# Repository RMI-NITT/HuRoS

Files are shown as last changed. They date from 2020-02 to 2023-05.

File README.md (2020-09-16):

# HuRoS
A 10 DoF Bipedal Walking robot, to be developed as a platform for further research on design and control of humanoid robots.

* 3D Printer -> Contains all the CAD files of the parts which were 3D printed for fabrication.
* CODES -> Contains all the motor control and simulation codes.
* References -> papers related to humaniod robots
* 100rpm_RMCS-3013.pdf;60rpm_RMCS-3012.pdf -> motors used in HuRoS-data sheet
* Dual_DC_Motor_Driver_20A.pdf -> motor drivers used 
* Biped Recent picture.jpeg -> complete fabrication 

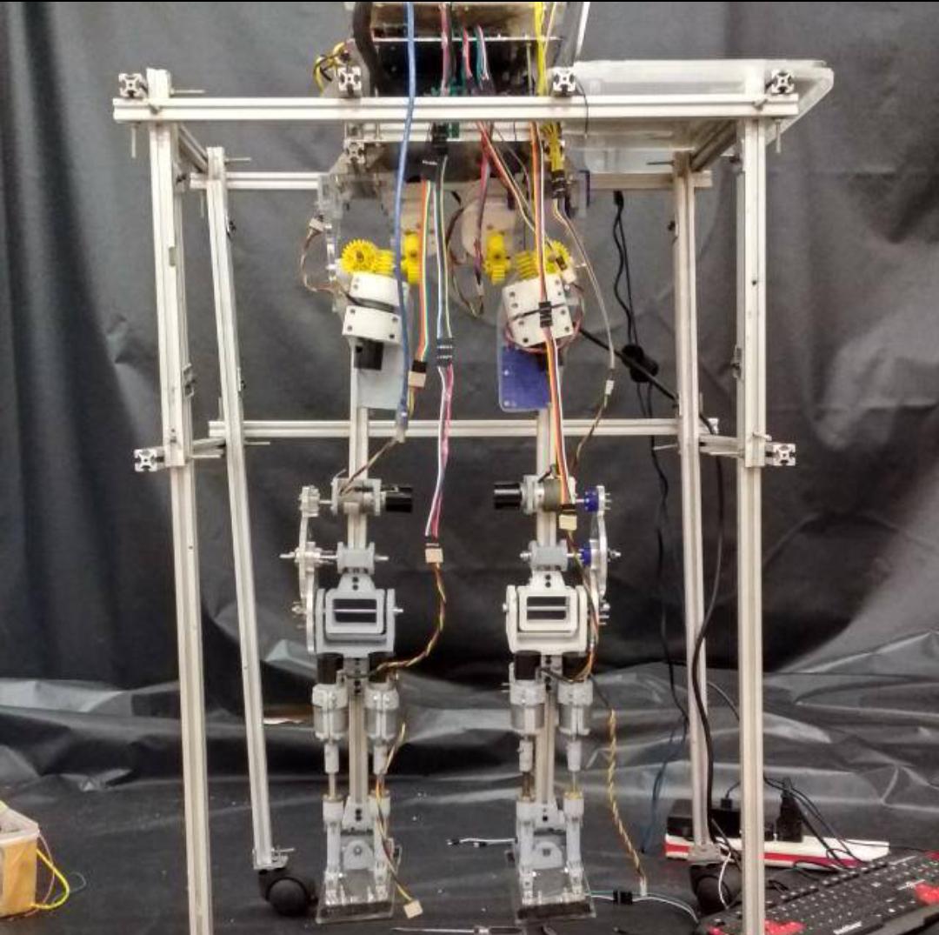
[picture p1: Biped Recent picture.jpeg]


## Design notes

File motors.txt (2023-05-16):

HuRoS motors and power supply

Rhino motor - RMCS 3013 DC geared motor with quad encoder, 100RPM 12V, 10 nos
Rated voltage - 12V, 
Running current - 0.8A/1.04A,
Starting peak current - 7.5A

Corsair VS550 power supply
GND the Green wire in motherboard connector for by-passing

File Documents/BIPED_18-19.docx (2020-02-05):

BIPED

Problem Statement

Simulate and fabricate bipedal robot which can walk over flat terrain by implementing CoM based and ZMP based control and stability techniques.

Tasks to be done

- Design an actuation mechanism for a universal joint. These types of joints are placed at each ankle and hip joints.
- Simulation of static stable gait in ROS-gazebo.
- Design and Fabrication of optimised model for improved agility and efficiency.
- Developing a dynamic model using Lagrangian mechanics.
- Simulation of dynamic gait using non-linear control strategies like SMC, Backstepping, etc

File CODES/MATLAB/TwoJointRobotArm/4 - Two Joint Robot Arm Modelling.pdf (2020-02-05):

## Two Joints Robot Arm Dynamics

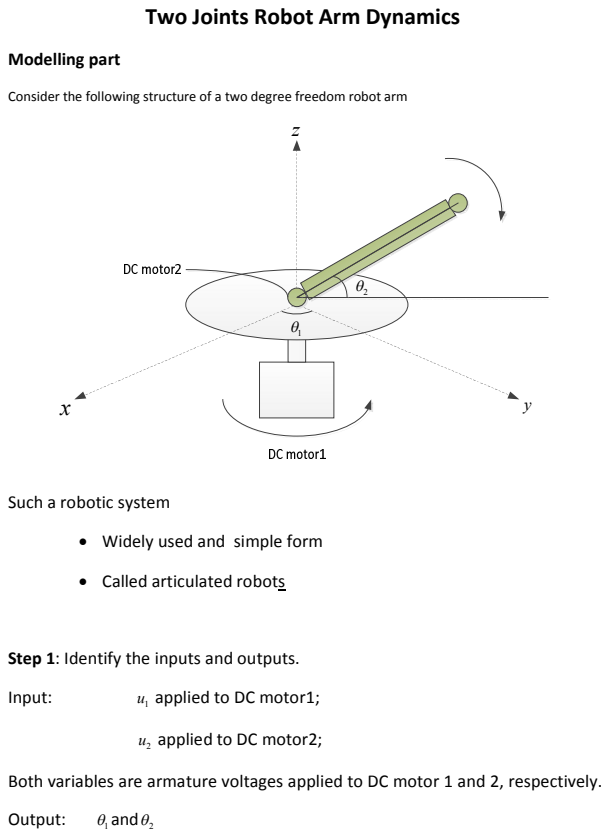
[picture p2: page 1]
Modelling part; Input:; Output:; θ1 andθ2

Consider the following structure of a two degree freedom robot arm

Such a robotic system

• Widely used and simple form

• Called articulated robots

Step 1: Identify the inputs and outputs.

u applied to DC motor1;

u applied to DC motor2;

Both variables are armature voltages applied to DC motor 1 and 2, respectively.

*Notations*

Shaft of DC motor1, it has a fixed part of the inertia 0

J that is obtained by

taking the arm away.

In terms of the robot arm, it has length H and mass m , i.e. { H , m } .

The parameters of the DC motors are given by:

DC motor1Þ | 1 | 1
1 | 1 | 1 | 2 { , , | , | } R L K K

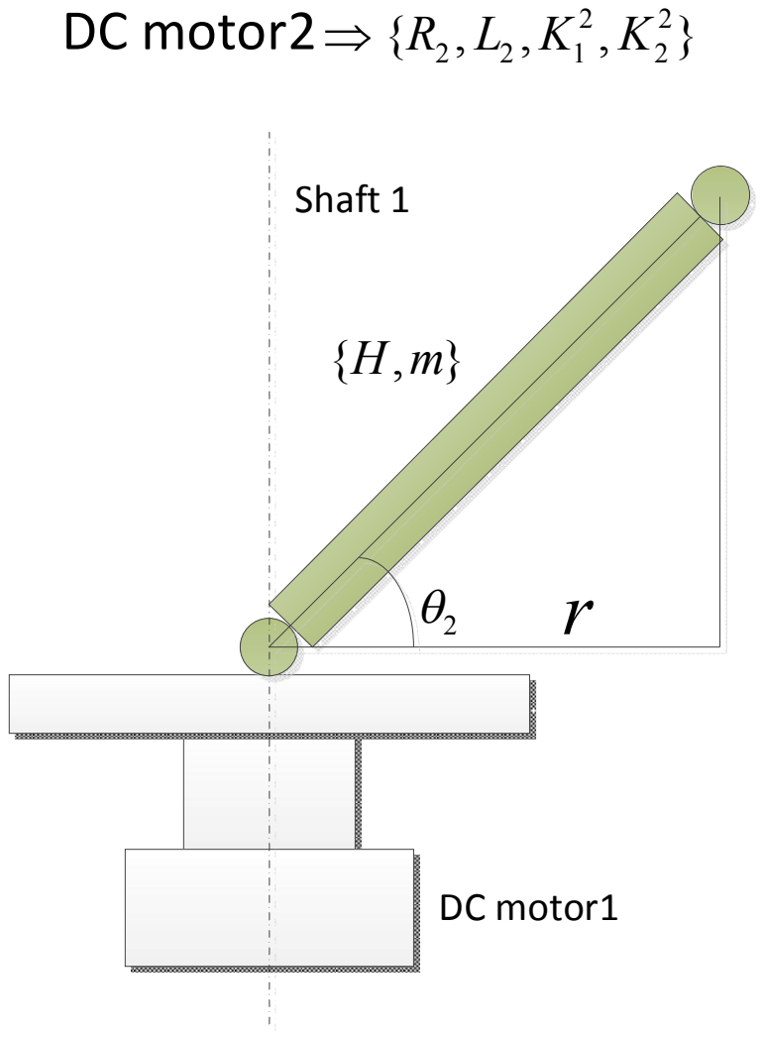
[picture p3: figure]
DC motor2Þ; Shaft 1; DC motor1

The equivalent inertia for the shaft driven by DC motor 1 is given by

2 | 2 | 2
0 | 0 | 2
1 | 1
cos
2 | 2
J | mr | J | mH + | = | + | θ | (1)

Therefore the mechanical equation for DC motor1 (shaft1) is

2
2 | 2 | 1 1
0 | 2 | 2 1 2

1
cos
2

d
J | mH | K i
dt

θ
θ
é | ù
+ | = ê | ú ë | û | (2)

where 1

i is the armature current of DC motor1.

1 | 1 1
1 1 | 1 | 1 | 1
di | d R i | L | K | u
dt | dt

θ
+ | + | = | (3)

Equation (3) is the electrical equation for the armature circuit of DC motor1.

Robot arm part modelling (DC motor2)

2
2 | 2
2 | 2 2 | 2 2
2 | 2 2
2 2 | 2 | 1 | 2

1
cos
2

d
J | K i | mHg
dt
di | d R i | L | K | u
dt | dt

θ
θ

θ

ì
= - ï
ï
í
ï | + | + | = ïî

(4)

Therefore the mechanical part of the model can be expressed as the following matrix form

2
1
2 | 2 | 1 2
0 | 2 | 2 | 1
2 | 2
2 | 2 | 2 | 2
2
2
1 | 0
cos | 0 | 0
( ) | 2 | 1
0 | cos 0 | 2

d
J | mH | dt | K | i
M q
d | K | i | Hmg J
| | dt θ
θ
θ | θ
é | ù é | ù | é | ù ê | ú + | é | ùé ù ê | ú | ê | ú = | = | + ê | ú ê | úê ú ê | úê | ú | ë û ê | ú - ë | û ë | û | ë | û ê | ú ë | û | (5)

In the course work the left hand side of the above equation is extended to: M (q,q) which is defined as inertia matrix for general multiple joint robot arm.

The above system can also be expressed as a state space form described before.

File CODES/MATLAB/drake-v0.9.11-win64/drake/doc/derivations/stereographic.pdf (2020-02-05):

## Stereographic Projection

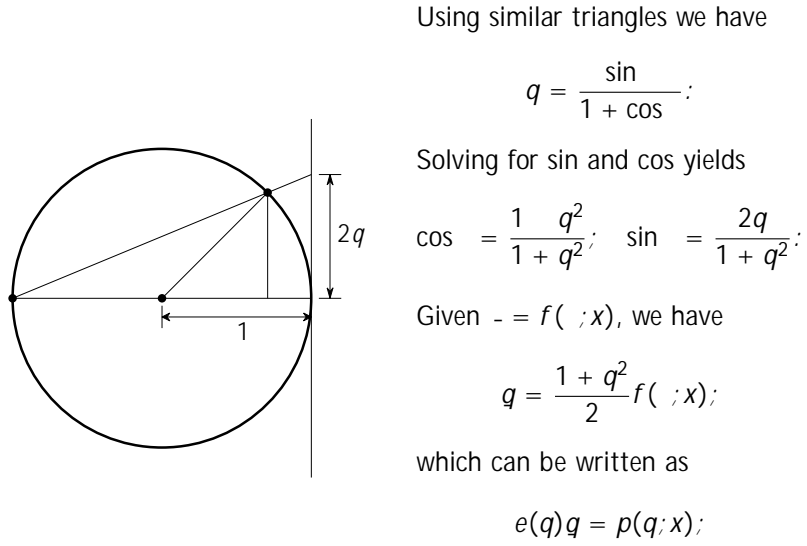
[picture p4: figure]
Using similar triangles we have; sin 1 + cos :; Solving for sin and cos yields; cos =; ; sin =; Given _ = f (; x), we have; which can be written as

with e() and p() polynomial in q.

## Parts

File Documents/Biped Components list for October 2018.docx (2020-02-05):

Biped Components list for October 2018

Component | Quantity | Cost per item | Cost | Link
Motor with encoders {HIGH TORQUE (35kgcm) QUAD ENCODER GEARED DC MOTOR 12V 100RPM} | 3 | 2124 | 6372 | https://robokits.co.in/motors/encoder-dc-servo/high-torque-quad-encoder-geared-dc-motor-12v-100rpm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
Motor driver {DUAL DC MOTOR DRIVER 20A} | 2 | 767 | 1534 | https://robokits.co.in/motor-drives/dual-dc-motor-driver-20a
Fabrication Parts (Aluminuim T Slot sections, L shaped aluminium reinforcements, 3 mm Aluminium 70755 Sheets, 3D printed parts,fasteners,etc) | | | 4000
Total | | | 11900

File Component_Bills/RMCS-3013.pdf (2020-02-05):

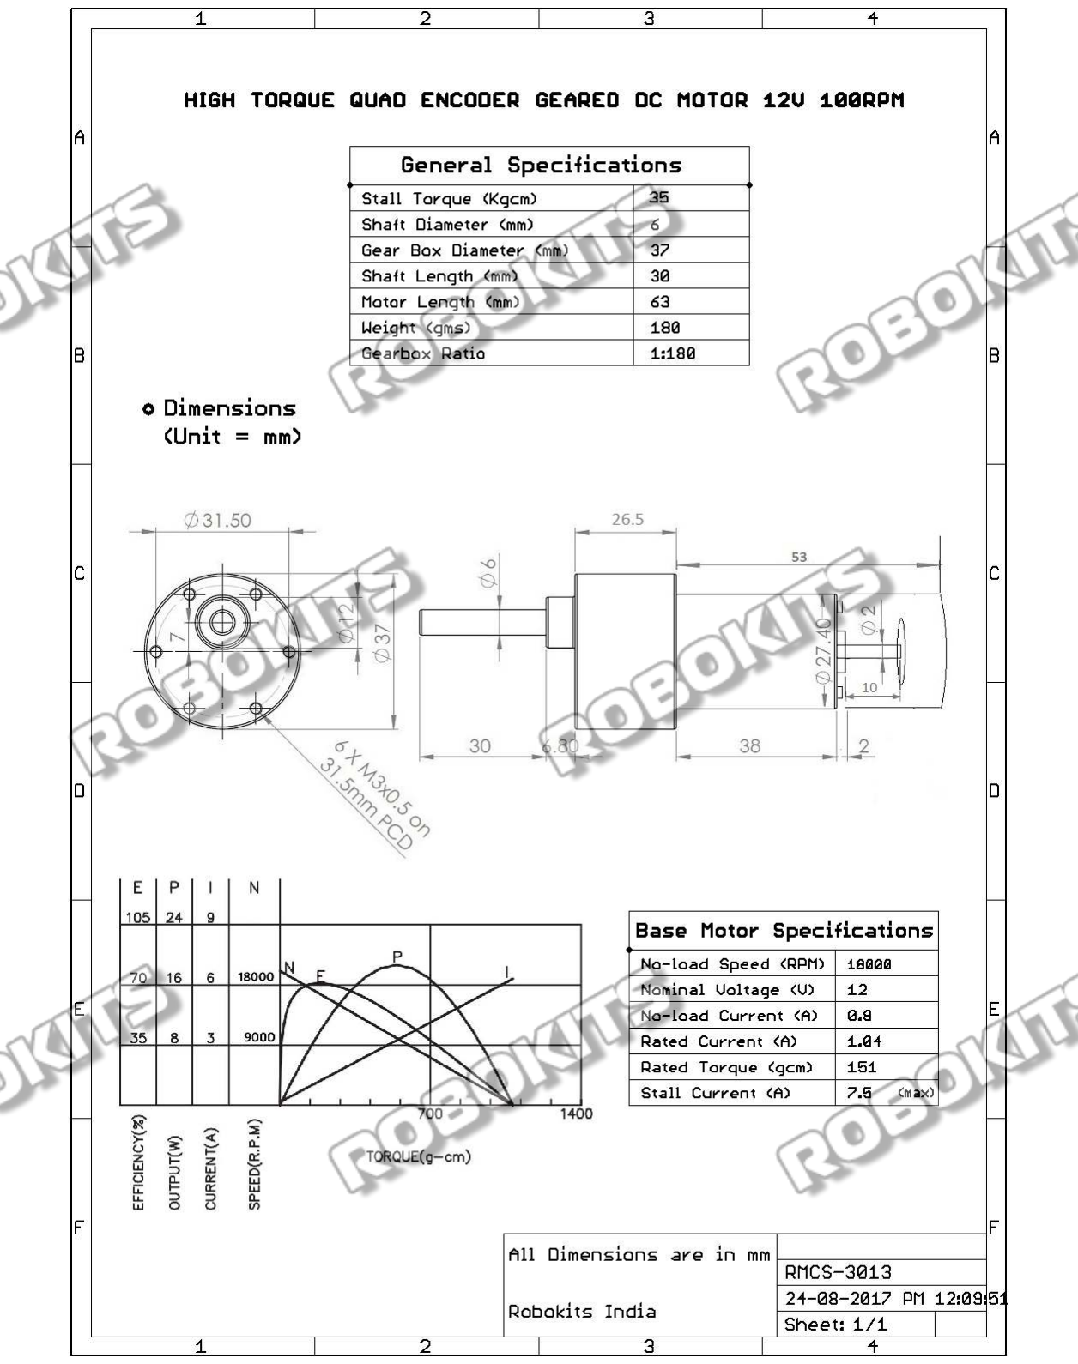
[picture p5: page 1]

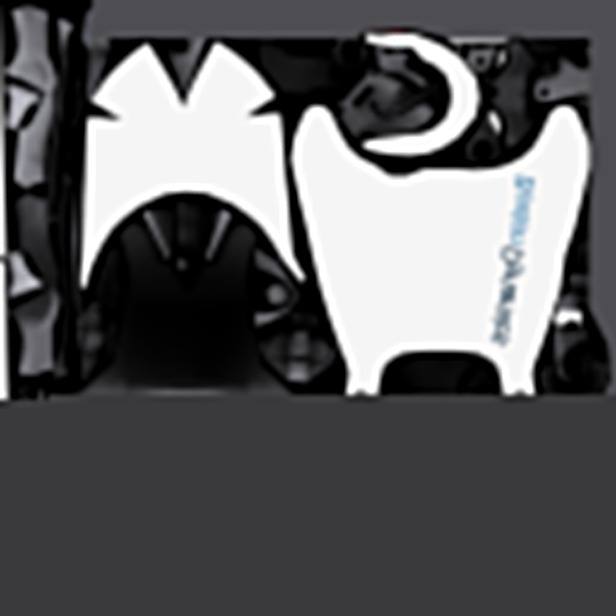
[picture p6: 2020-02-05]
CODES/MATLAB/drake-v0.9.11-win64/drake/examples/Atlas/urdf/materials/textures/right_leg_diffuse_unplugged.jpg

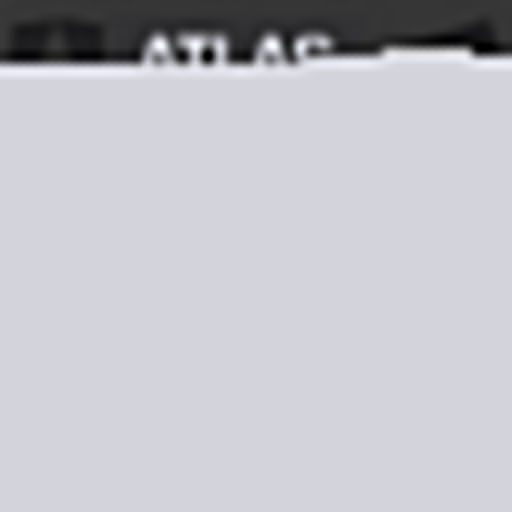
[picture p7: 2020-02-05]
CODES/MATLAB/drake-v0.9.11-win64/drake/examples/Atlas/urdf/materials/textures/drc_labels_1.jpg

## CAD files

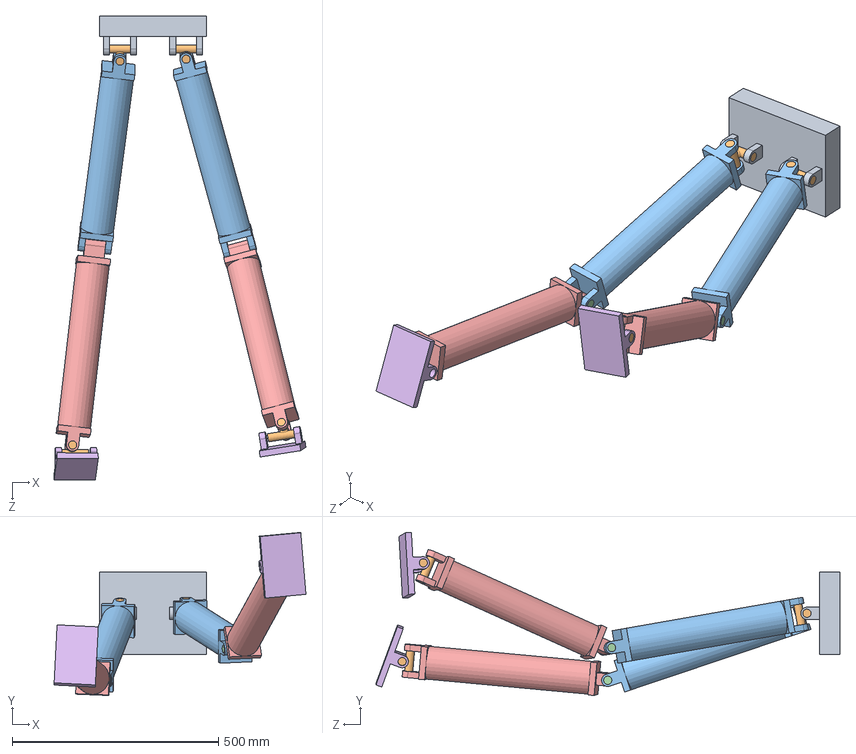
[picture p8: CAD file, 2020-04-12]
CODES/Simulation/FULL_BIPED.SLDASM
610.4 x 395.0 x 1124.1 mm
hip
spider_univ_8 x 4
thigh x 2
revolute x 2
calf x 2
foot x 2

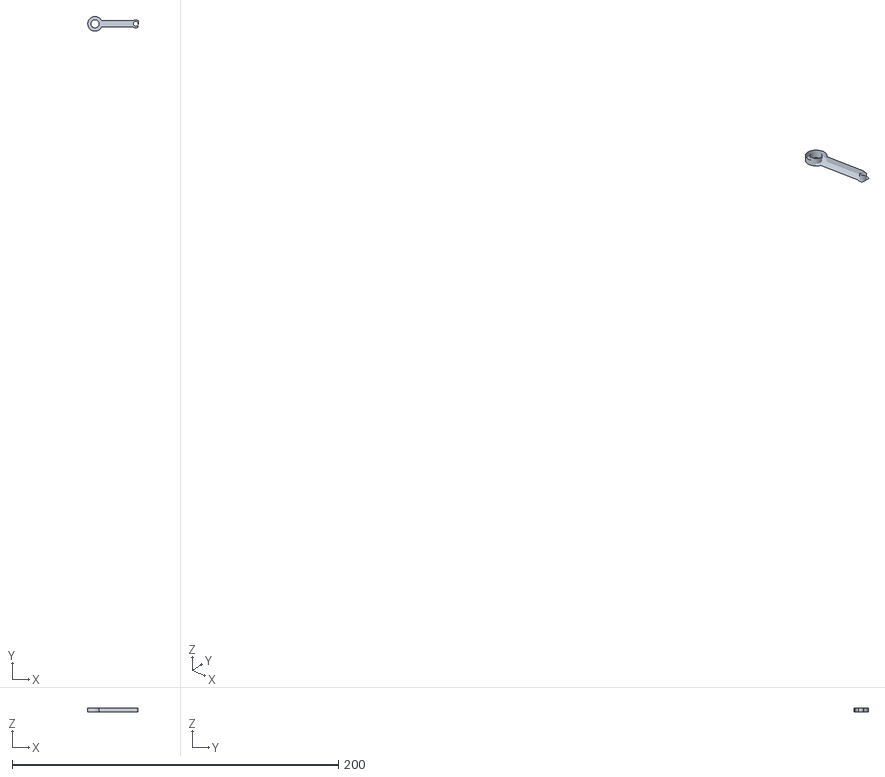
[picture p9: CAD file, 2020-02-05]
3D Printer/1.stl
36.1 x 388.8 x 3.50

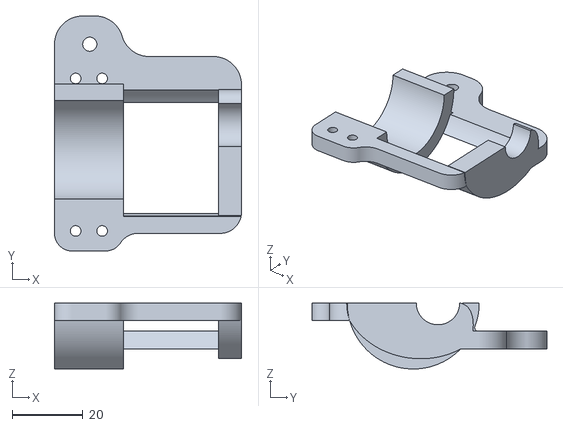
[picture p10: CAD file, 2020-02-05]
3D Printer/3d parts_new/module_7_link3_3_tol1.prt.stl
53.0 x 66.6 x 18.7

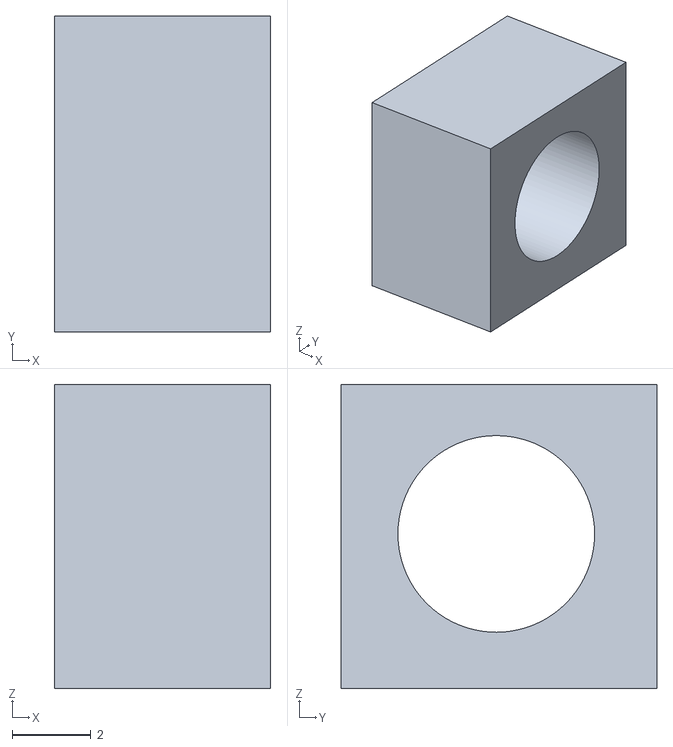
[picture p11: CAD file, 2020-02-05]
3D Printer/test/hole_test.stl
5.50 x 8.03 x 7.73

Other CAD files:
Design/Creo Files/biped2_0/FOOT/foot1_asm.igs
Design/module_1/module_3_asm.igs
3D Printer/3dPriningfiles/toe.stl
ANALYSIS/SYS-2.igs
biped_27.2/bipconfig/primary_link_ul_prt.step
biped_27.2/biped_1/link_base_1_prt.step
biped_27.2/biped_woa1/servo_prt.step
biped_27.2/bipedtrial_3/ft_prt.step
biped_27.2/New Folder/motor_connector_prt.step
CODES/MATLAB/biped _woa1_backup/support_link1_prt.step
CODES/MATLAB/biped trial/ji_prt.step
CODES/MATLAB/biped trial1a/handle22_prt.step
CODES/MATLAB/biped trial2/jil_prt.step
CODES/MATLAB/biped_1/tarsal_link_prt.step
3D Printer/3dPriningfiles/tray0001.stl
3D Printer/3dp_link1.stl
3D Printer/3dp_link2.stl
3D Printer/module_7_link4.stl
3D Printer/toe.stl
3D Printer/tray0001.stl
CODES/MATLAB/biped _woa1_backup/ball_bearing_prt.step
CODES/MATLAB/biped _woa1_backup/base1_prt.step
CODES/MATLAB/biped _woa1_backup/hip_shaft1_connector_prt.step
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

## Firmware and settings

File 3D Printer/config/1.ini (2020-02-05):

# generated by Slic3r 1.3.1-dev on Mon Dec 24 19:01:29 2018

[filament:1]
bed_temperature = 80
bridge_fan_speed = 50
compatible_printers = 
cooling = 1
disable_fan_first_layers = 3
end_filament_gcode = "; Filament-specific end gcode \n;END gcode for filament\n"
extrusion_multiplier = 1
fan_always_on = 1
fan_below_layer_time = 60
filament_colour = #000000
filament_cost = 1000
filament_density = 1.25
filament_diameter = 1.9
filament_max_volumetric_speed = 0
filament_notes = ""
filament_settings_id = 
first_layer_bed_temperature = 80
first_layer_temperature = 230
max_fan_speed = 100
min_fan_speed = 25
min_print_speed = 10
slowdown_below_layer_time = 20
start_filament_gcode = "; Filament gcode\n"
temperature = 235
wipe = 1

[filament:My Settings]
bed_temperature = 0
bridge_fan_speed = 100
compatible_printers = 
cooling = 1
disable_fan_first_layers = 3
end_filament_gcode = "; Filament-specific end gcode \n;END gcode for filament\n"
extrusion_multiplier = 1
fan_always_on = 0
fan_below_layer_time = 60
filament_colour = #FFFFFF
filament_cost = 0
filament_density = 0
filament_diameter = 1.75
filament_max_volumetric_speed = 0
filament_notes = ""
filament_settings_id = 
first_layer_bed_temperature = 0
first_layer_temperature = 205
max_fan_speed = 100
min_fan_speed = 35
min_print_speed = 10
slowdown_below_layer_time = 5
start_filament_gcode = "; Filament gcode\n"
temperature = 200

[presets]
filament = 1
print = 1
printer = 1

[print:1]
adaptive_slicing = 0
adaptive_slicing_quality = 79%
avoid_crossing_perimeters = 0
bottom_infill_pattern = rectilinear
bottom_solid_layers = 5
bridge_acceleration = 0
bridge_flow_ratio = 0.9
bridge_speed = 25
brim_connections_width = 3
brim_width = 5
compatible_printers = 
complete_objects = 0
default_acceleration = 0
dont_support_bridges = 0
external_perimeter_extrusion_width = 0.4
external_perimeter_speed = 25
external_perimeters_first = 0
extra_perimeters = 1
extruder_clearance_height = 20
extruder_clearance_radius = 20
extrusion_width = 0.4
fill_angle = 45
fill_density = 100%
fill_gaps = 1
fill_pattern = rectilinear
first_layer_acceleration = 0
first_layer_extrusion_width = 0.4
first_layer_height = 0.2
first_layer_speed = 60%
gap_fill_speed = 25
gcode_comments = 0
infill_acceleration = 0
infill_every_layers = 1
infill_extruder = 1
infill_extrusion_width = 0.5
infill_first = 0
infill_only_where_needed = 1
infill_overlap = 60%
infill_speed = 35
interface_shells = 0
interior_brim_width = 5
label_printed_objects = 0
layer_height = 0.15
match_horizontal_surfaces = 0
max_print_speed = 80
max_volumetric_speed = 0
min_shell_thickness = 0
min_skirt_length = 0
min_top_bottom_shell_thickness = 0
notes = 
only_retract_when_crossing_perimeters = 0
ooze_prevention = 0
output_filename_format = [input_filename_base].gcode
overhangs = 1
perimeter_acceleration = 0
perimeter_extruder = 1
perimeter_extrusion_width = 0.4
perimeter_speed = 30
perimeters = 3
post_process = 
print_settings_id = 
raft_layers = 0
regions_overlap = 0
resolution = 0
seam_position = aligned
shortcuts = bridge_flow_ratio;extrusion_width;infill_extrusion_width;perimeter_extrusion_width;adaptive_slicing_quality;avoid_crossing_perimeters;thin_walls;support_material
skirt_distance = 3
skirt_height = 1
skirts = 3
small_perimeter_speed = 30
solid_infill_below_area = 25
solid_infill_every_layers = 0
solid_infill_extruder = 1
solid_infill_extrusion_width = 0.5
solid_infill_speed = 35
spiral_vase = 0
standby_temperature_delta = -5
support_material = 1
support_material_angle = 0
support_material_buildplate_only = 0
support_material_contact_distance = 0.15
support_material_enforce_layers = 0
support_material_extruder = 1
support_material_extrusion_width = 0.4
support_material_interface_extruder = 1
support_material_interface_extrusion_width = 0.4
support_material_interface_layers = 3
support_material_interface_spacing = 0.1
support_material_interface_speed = 35
support_material_max_layers = 0
support_material_pattern = pillars
support_material_pillar_size = 3
support_material_pillar_spacing = 15
support_material_spacing = 4
support_material_speed = 40
support_material_threshold = 35
thin_walls = 1
top_infill_extrusion_width = 0.5
top_infill_pattern = rectilinear
top_solid_infill_speed = 35
top_solid_layers = 5
travel_speed = 120
xy_size_compensation = 0

[print:2]
adaptive_slicing = 0
adaptive_slicing_quality = 79%
avoid_crossing_perimeters = 0
bottom_infill_pattern = rectilinear
bottom_solid_layers = 5
bridge_acceleration = 0
bridge_flow_ratio = 1.2
bridge_speed = 15
brim_connections_width = 0
brim_width = 0
compatible_printers = 
complete_objects = 0
default_acceleration = 0
dont_support_bridges = 0
external_perimeter_extrusion_width = 0.4
external_perimeter_speed = 40
external_perimeters_first = 1
extra_perimeters = 1
extruder_clearance_height = 20
extruder_clearance_radius = 20
extrusion_width = 0.4
fill_angle = 45
fill_density = 60%
fill_gaps = 1
fill_pattern = rectilinear
first_layer_acceleration = 0
first_layer_extrusion_width = 0.4
first_layer_height = 0.2
first_layer_speed = 60%
gap_fill_speed = 45
gcode_comments = 0
infill_acceleration = 0
infill_every_layers = 5
infill_extruder = 1
infill_extrusion_width = 0.5
infill_first = 0
infill_only_where_needed = 0
infill_overlap = 60%
infill_speed = 45
interface_shells = 0
interior_brim_width = 0
label_printed_objects = 0
layer_height = 0.22
match_horizontal_surfaces = 0
max_print_speed = 80
max_volumetric_speed = 0
min_shell_thickness = 0
min_skirt_length = 0
min_top_bottom_shell_thickness = 0
notes = 
only_retract_when_crossing_perimeters = 0
ooze_prevention = 0
output_filename_format = [input_filename_base].gcode
overhangs = 1
perimeter_acceleration = 0
perimeter_extruder = 1
perimeter_extrusion_width = 0.4
perimeter_speed = 40
perimeters = 2
post_process = 
print_settings_id = 
raft_layers = 0
regions_overlap = 0
resolution = 0
seam_position = aligned
shortcuts = bridge_flow_ratio;extrusion_width;infill_extrusion_width;perimeter_extrusion_width;adaptive_slicing_quality;avoid_crossing_perimeters;thin_walls;support_material
skirt_distance = 3
skirt_height = 1
skirts = 3
small_perimeter_speed = 40
solid_infill_below_area = 30
solid_infill_every_layers = 5
solid_infill_extruder = 1
solid_infill_extrusion_width = 0.5
solid_infill_speed = 45
spiral_vase = 0
standby_temperature_delta = -5
support_material = 0
support_material_angle = 0
support_material_buildplate_only = 0
support_material_contact_distance = 0.2
support_material_enforce_layers = 0
support_material_extruder = 1
support_material_extrusion_width = 0.4
support_material_interface_extruder = 1
support_material_interface_extrusion_width = 0.4
support_material_interface_layers = 3
support_material_interface_spacing = 0
support_material_interface_speed = 30
support_material_max_layers = 0
support_material_pattern = pillars
support_material_pillar_size = 2.5
support_material_pillar_spacing = 10
support_material_spacing = 2.5
support_material_speed = 30
support_material_threshold = 45
thin_walls = 1
top_infill_extrusion_width = 0.5
top_infill_pattern = rectilinear
top_solid_infill_speed = 45
top_solid_layers = 5
travel_speed = 100
xy_size_compensation = 0
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

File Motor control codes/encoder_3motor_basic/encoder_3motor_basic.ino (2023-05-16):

// Basic code for running 3 motors forward and backward, and getting the encoder count

#define MOT1_DIR  35   // Motor1 direction pin
#define MOT1_BRK  41   // Motor1 brake pin
#define MOT2_DIR  37   // Motor2 direction pin
#define MOT2_BRK  43   // Motor2 brake pin
#define MOT3_DIR  39   // Motor3 direction pin
#define MOT3_BRK  45   // Motor3 brake pin

#define MOT1_PWM  5   // Motor 1 PWM pin
#define MOT2_PWM  6   // Motor 2 PWM pin
#define MOT3_PWM  7   // Motor 3 PWM pin

int MOT1_ECA = 20;   // Motor 1 encoder A pin
int MOT1_ECB = 21;   // Motor 1 encoder B pin
int MOT2_ECA = 18;   // Motor 2 encoder A pin
int MOT2_ECB = 19;   // Motor 2 encoder B pin
int MOT3_ECA = 2;   // Motor 3 encoder A pin
int MOT3_ECB = 3;   // Motor 3 encoder B pin

volatile int lastEncoded1 = 0, lastEncoded2 = 0, lastEncoded3 = 0; // Here updated value of encoder store.
volatile long encoderValue1 = 0, encoderValue2 = 0, encoderValue3 = 0; // Raw encoder value

int MSB, LSB, encoded, sum;
void setup() {

  pinMode(MOT1_DIR, OUTPUT); 
  pinMode(MOT2_DIR, OUTPUT); 
  pinMode(MOT3_DIR, OUTPUT); 
  pinMode(MOT1_BRK, OUTPUT); 
  pinMode(MOT2_BRK, OUTPUT); 
  pinMode(MOT3_BRK, OUTPUT);
  pinMode(MOT1_PWM, OUTPUT);
  pinMode(MOT2_PWM, OUTPUT);
  pinMode(MOT3_PWM, OUTPUT);
  
  Serial.begin(9600); //initialize serial comunication
  
  pinMode(MOT1_ECA, INPUT_PULLUP);
  pinMode(MOT1_ECB, INPUT_PULLUP);
  pinMode(MOT2_ECA, INPUT_PULLUP);
  pinMode(MOT2_ECB, INPUT_PULLUP);
  pinMode(MOT3_ECA, INPUT_PULLUP);
  pinMode(MOT3_ECB, INPUT_PULLUP); 

  digitalWrite(MOT1_ECA, HIGH); //turn pullup resistor on
  digitalWrite(MOT1_ECB, HIGH); //turn pullup resistor on
  digitalWrite(MOT2_ECA, HIGH); //turn pullup resistor on
  digitalWrite(MOT2_ECB, HIGH); //turn pullup resistor on
  digitalWrite(MOT3_ECA, HIGH); //turn pullup resistor on
  digitalWrite(MOT3_ECB, HIGH); //turn pullup resistor on

  attachInterrupt(2, updateEncoder1, CHANGE); 
  attachInterrupt(3, updateEncoder1, CHANGE);
  attachInterrupt(4, updateEncoder2, CHANGE); 
  attachInterrupt(5, updateEncoder2, CHANGE);
  attachInterrupt(0, updateEncoder3, CHANGE); 
  attachInterrupt(1, updateEncoder3, CHANGE); 

//  digitalWrite(MOT1_PWM,HIGH);
//  digitalWrite(MOT2_PWM,HIGH);
//  digitalWrite(MOT3_PWM,HIGH);
  analogWrite(MOT1_PWM,100);
  analogWrite(MOT2_PWM,100);
  analogWrite(MOT3_PWM,100);
}

void loop() {
  digitalWrite(MOT1_BRK, LOW);
  digitalWrite(MOT2_BRK, LOW);
  digitalWrite(MOT3_BRK, LOW);
  
  digitalWrite(MOT1_DIR, HIGH); 
  digitalWrite(MOT2_DIR, HIGH);
  digitalWrite(MOT3_DIR, HIGH);
  for (int i = 0; i <= 300; i++){
    Serial.print(encoderValue1);
    Serial.print(" | ");
    Serial.print(encoderValue2);
    Serial.print(" | ");
    Serial.println(encoderValue3);
}
  digitalWrite(MOT1_BRK, HIGH);
  digitalWrite(MOT2_BRK, HIGH);
  digitalWrite(MOT3_BRK, HIGH);
  
  delay(2000);
  
  digitalWrite(MOT1_BRK, LOW);
  digitalWrite(MOT2_BRK, LOW);
  digitalWrite(MOT3_BRK, LOW);
  digitalWrite(MOT1_DIR, LOW); 
  digitalWrite(MOT2_DIR, LOW);
  digitalWrite(MOT3_DIR, LOW);
  
  for (int i = 0; i <= 300; i++){
    Serial.print(encoderValue1);
    Serial.print(" | ");
    Serial.print(encoderValue2);
    Serial.print(" | ");
    Serial.println(encoderValue3);
}
  digitalWrite(MOT1_BRK, HIGH);
  digitalWrite(MOT2_BRK, HIGH); 
  digitalWrite(MOT3_BRK, HIGH);
    
  delay(2000);
} 

void updateEncoder1(){
//  Serial.println("ENCODER1");
  MSB = digitalRead(MOT1_ECA); //MSB = most significant bit
  LSB = digitalRead(MOT1_ECB); //LSB = least significant bit

  encoded = (MSB << 1) |LSB; //converting the 2 pin value to single number
  sum  = (lastEncoded1 << 2) | encoded; //adding it to the previous encoded value

  if(sum == 0b1101 || sum == 0b0100 || sum == 0b0010 || sum == 0b1011) encoderValue1 --;
  if(sum == 0b1110 || sum == 0b0111 || sum == 0b0001 || sum == 0b1000) encoderValue1 ++;

  lastEncoded1 = encoded; //store this value for next time

}

void updateEncoder2(){
//  Serial.println("ENCODER2");
  MSB = digitalRead(MOT2_ECA); //MSB = most significant bit
  LSB = digitalRead(MOT2_ECB); //LSB = least significant bit

  encoded = (MSB << 1) |LSB; //converting the 2 pin value to single number
  sum  = (lastEncoded2 << 2) | encoded; //adding it to the previous encoded value

  if(sum == 0b1101 || sum == 0b0100 || sum == 0b0010 || sum == 0b1011) encoderValue2 --;
  if(sum == 0b1110 || sum == 0b0111 || sum == 0b0001 || sum == 0b1000) encoderValue2 ++;

  lastEncoded2 = encoded; //store this value for next time

}

void updateEncoder3(){
//  Serial.println("ENCODER3");

  MSB = digitalRead(MOT3_ECA); //MSB = most significant bit
  LSB = digitalRead(MOT3_ECB); //LSB = least significant bit

  encoded = (MSB << 1) |LSB; //converting the 2 pin value to single number
  sum  = (lastEncoded3 << 2) | encoded; //adding it to the previous encoded value

  if(sum == 0b1101 || sum == 0b0100 || sum == 0b0010 || sum == 0b1011) encoderValue3 --;
  if(sum == 0b1110 || sum == 0b0111 || sum == 0b0001 || sum == 0b1000) encoderValue3 ++;

  lastEncoded3 = encoded; //store this value for next time

}

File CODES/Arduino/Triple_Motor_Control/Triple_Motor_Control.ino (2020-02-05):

/* Encoder Library - TwoKnobs Example
 * http://www.pjrc.com/teensy/td_libs_Encoder.html
 *
 * This example code is in the public domain.
 */

#include <Encoder.h>

// Change these pin numbers to the pins connected to your encoder.
//   Best Performance: both pins have interrupt capability
//   Good Performance: only the first pin has interrupt capability
//   Low Performance:  neither pin has interrupt capability
Encoder motorLeft(2,3);
Encoder motorRight(18,19);
int dirPin1=38, pwmPin1=7, dirPin2=36, pwmPin2=6;
long integral1=0,integral2=0;
long eAngle1=0, eAngle2=0;
//double kp = 0.0025, ki = 0.00001;
double kp = 0.003, ki = 0.00015;
#define LEFT 0
#define RIGHT 1
long encoderConstant = 29520/360; //Counts per revolution for 100RPM motor
//   avoid using pins with LEDs attached

void setup() {
  Serial.begin(9600);
  Serial.println("Encoder Test:");
  pinMode(dirPin1, OUTPUT);
  pinMode(pwmPin1, OUTPUT);
  pinMode(dirPin2, OUTPUT);
  pinMode(pwmPin2, OUTPUT);
}

long positionLeft  = -999;
long positionRight = -999;

int posControl1(long error){
  long pwm=0;
 // double kp = 0.0025, ki = 0.00008;
  int dir;
  
  if(abs(error)<25000){
  integral1 = integral1 + error;
  }  
  //Serial.print("error:");
  //Serial.print(error/encoderConstant);

  if (abs(error)<2*encoderConstant){   // 2 degree error
    integral1=0;
  }
  pwm = int(kp*error + ki*integral1);
   
  if(pwm<0){
    dir=LEFT;
  }
  else{
    dir=RIGHT;
  }
  pwm=abs(pwm);
  if(pwm>255){
    pwm=255;
  }
  
  //Serial.print("PWM:");
  //Serial.println(pwm);
  
  digitalWrite(dirPin1, dir);
  analogWrite(pwmPin1, pwm);
  //Serial.print("Dir:");
  //Serial.println(dir);
 // Serial.println("Run");
  return 0;
}

int posControl2(long error){
  long pwm=0;
  //double kp = 0.0015, ki = 0.00001;
  int dir;
  
  if(abs(error)<25000){
  integral2 = integral2 + error;
  
  }

  /*
  Serial.print("error:");
  Serial.print(error/encoderConstant);

  
  Serial.print(" integral:");
  Serial.println(integral);
  */
  if (abs(error)<2*encoderConstant){   // 2 degree error
    integral2=0;
  }
  
  pwm = int(kp*error + ki*integral2);
  
  
  if(pwm<0){
    dir=LEFT;
  }
  else{
    dir=RIGHT;
  }
  pwm=abs(pwm);
  if(pwm>255){
    pwm=255;
  }
  /*
  if (abs(diff) < 40*encoderConstant && abs(diff)>0){
    //Serial.println("low");
    pwm=20;
  }
  else{
    pwm=abs(diff)/200;
  }
  
  
  Serial.print("PWM:");
  Serial.println(pwm);
  */
  digitalWrite(dirPin2, dir);
  analogWrite(pwmPin2, pwm);
  //Serial.print("Dir:");
  //Serial.println(dir);
 // Serial.println("Run");
  return 0;
  }

void loop() {
  long newLeft, newRight,error;
  long angle;
  String angleStr;
  newLeft = motorLeft.read();
  newRight = motorRight.read();
  if (newLeft != positionLeft || newRight != positionRight) {
    Serial.print("Left = ");
    Serial.print(newLeft/encoderConstant);
    Serial.print(", Right = ");
    Serial.print(newRight/encoderConstant);
    //Serial.print(" error:");
  //Serial.print(error);
  //Serial.print(" integral:");
  //Serial.println(integral);
    Serial.println(" Wait....");
    positionLeft = newLeft;
    positionRight = newRight;
  }
  //Serial.flush();
  // angle reading from serial monitor
  if (Serial.available()) {
    //Serial.println("Reading....");
    angleStr=Serial.readStringUntil(',');
    angle=angleStr.toInt();
    Serial.println(angle);
    //Serial.flush();
    eAngle1=angle*encoderConstant;
    
    angleStr=Serial.readStringUntil(';');
    angle=angleStr.toInt();
    Serial.println(angle);
    //Serial.flush();
    eAngle2=angle*encoderConstant;
    
    //Serial.print("Angle:");
    //Serial.println(angle);
    //knobLeft.write(0);
    //knobRight.write(0);
  }
  error=eAngle1-newLeft;
  posControl1(error);
  
  error=eAngle2-newRight;
  //Serial.println(error);
  posControl2(error);
}

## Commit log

2020-02-25 changed: pins, pid constants
    changed the pin nos according to the PCB board; PID constant values were updated according to the ankle range motion
2020-02-25 changed pid constants at knee motor
    changed PID constants for the knee angle range; need to test and update the encoder pins to 2 &3 MD 3, currently tested in MD 2
2020-04-26 JSON Board
    [Biped Motor Control Board.json]
2023-05-16 Added motors data and PCB pin connections
2023-05-16 Motor control codes
2023-05-16 Rename PID_basic/PID_basic.ino to Motor control codes/PID_basic/PID_basic.ino
